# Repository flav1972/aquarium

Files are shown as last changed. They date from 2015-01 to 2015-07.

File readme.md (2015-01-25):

Aquarium controler
==================

Project Homepage: http://wiki.flav.com/wiki/Aquarium_Controller

Repository Contents
-------------------

* **/** - The root directory contains the arduino sketch
* **/hardware** - All hardware design files
* **/software** - Libraries used and hardwares sketch tests
* **/other** - Calculation and documentation files

Usage
-----

The project needs to be in a "aquarium" directory.

The main file is aquarium.ino. This is the file that has to be opened with Arduino IDE.

Edit setups in globals.h.

License Information
-------------------
The hardware is released under [Creative Commons Share-alike 3.0](http://creativecommons.org/licenses/by-sa/3.0/).  
The firmware is released under the [MIT License](http://opensource.org/licenses/MIT).

Author: Flavius Bindea

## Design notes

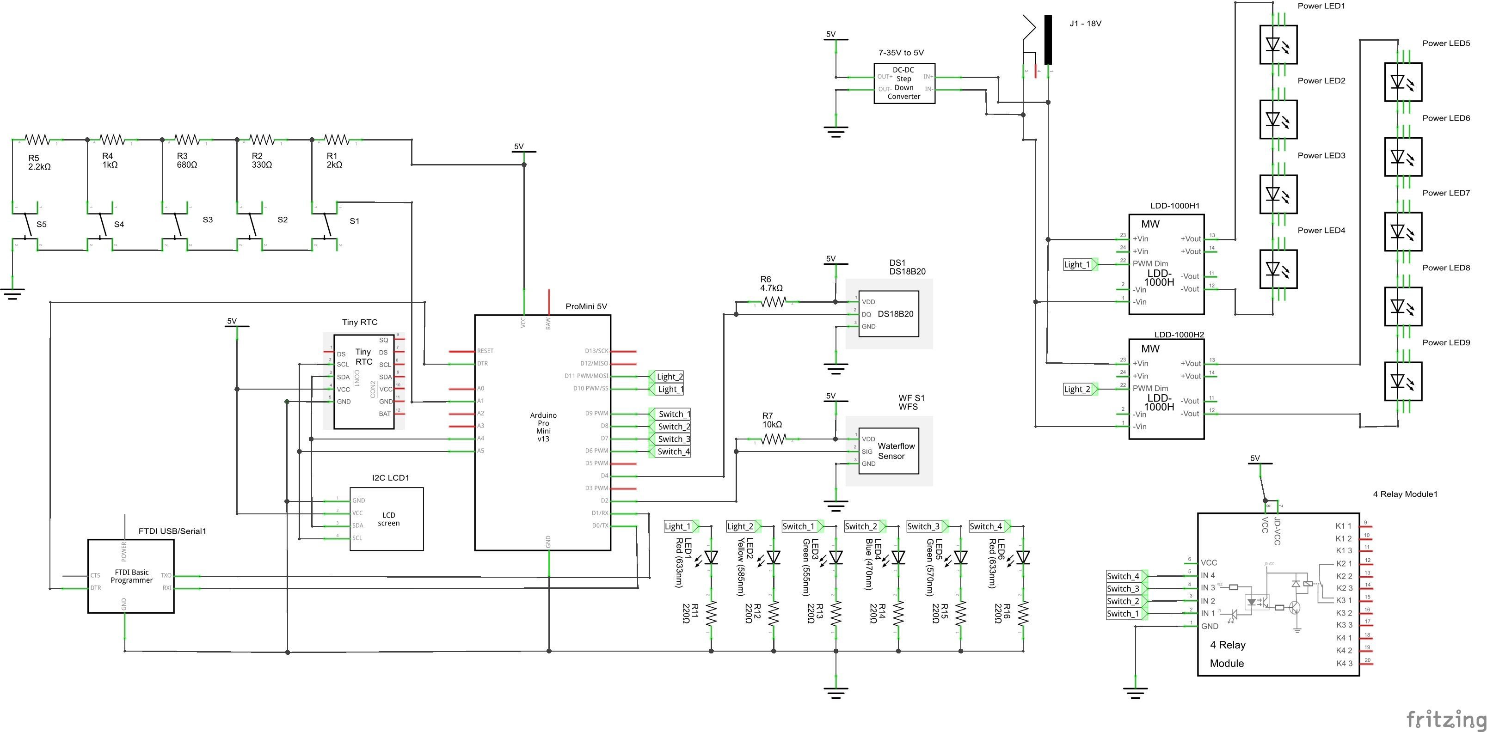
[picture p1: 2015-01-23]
hardware/aquarium_schema.png

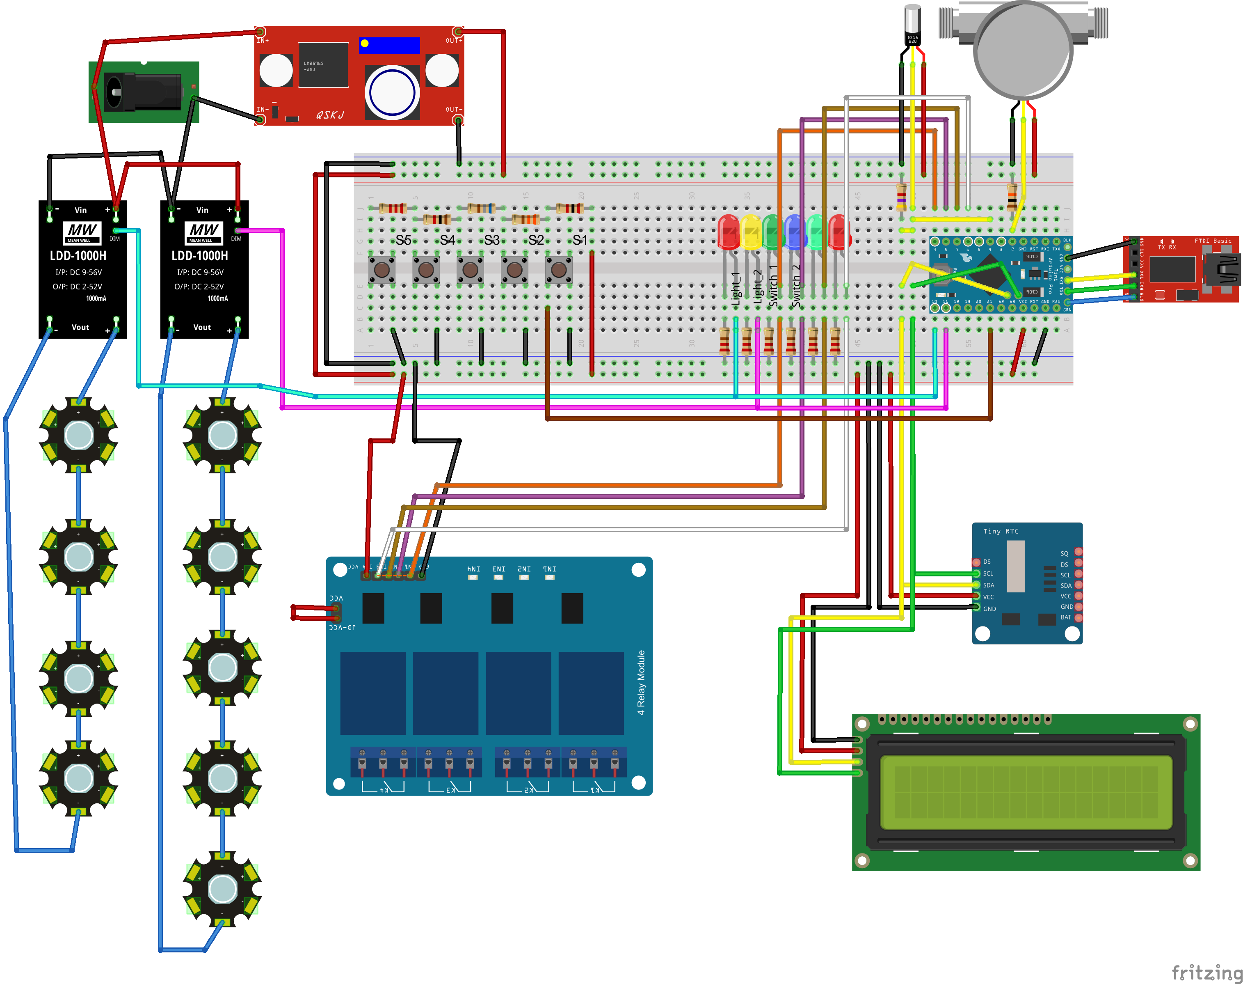
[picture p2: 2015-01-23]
hardware/aquarium_bb.png

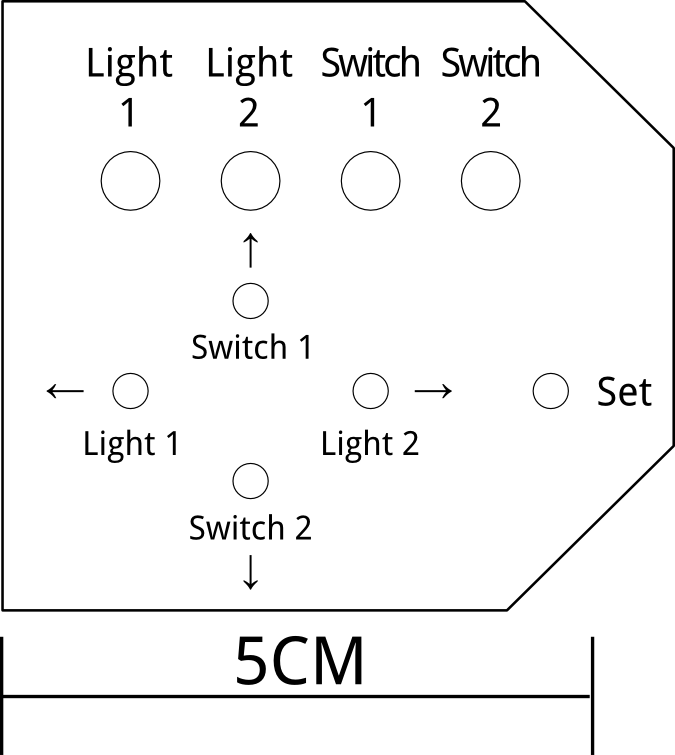
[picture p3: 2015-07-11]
other/front_pannel_labels.png

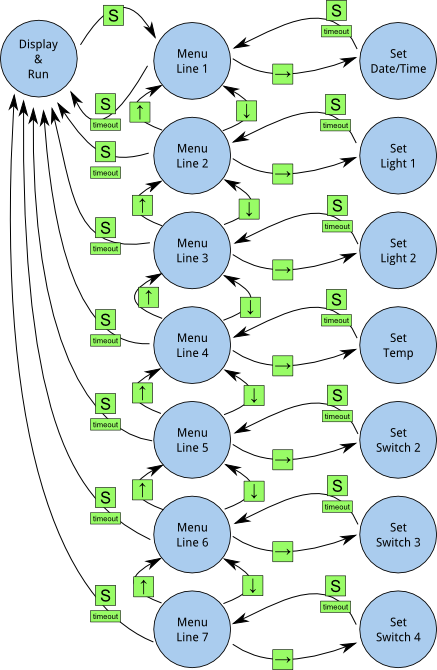
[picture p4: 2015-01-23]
other/menu.png

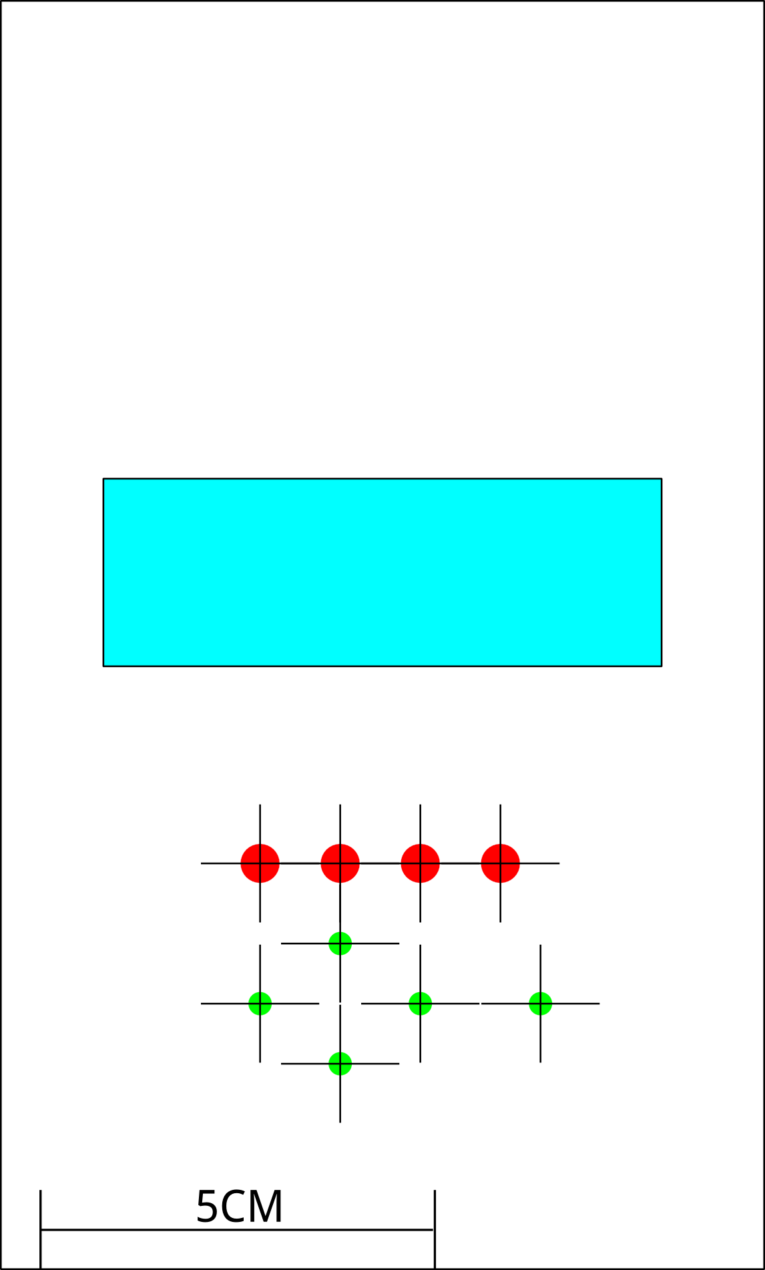
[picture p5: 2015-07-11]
other/front_pannel.png

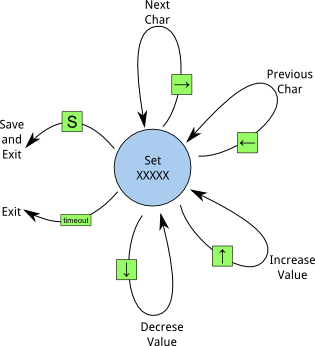
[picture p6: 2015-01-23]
other/menu_detail.png

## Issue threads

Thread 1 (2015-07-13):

DS18B20 fails after a few hours

flav1972, 2015-07-13:
The DS18B20 fails to send temperature after a few hours.
It looks like the same issue as this: http://forum.arduino.cc/index.php?topic=75757.0

The last commit about temperature does not solves the issue, neither the watchdog.

Need to implement cut/restart of power on the OneWire bus.

flav1972, 2016-01-28:
Fail is due to electric interferance with 220V motor near the controler.

Closed 2016-01-28.

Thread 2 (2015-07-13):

ERROR: temperature expired is never reached

flav1972, 2015-07-13:
It looks like : the following test is not correct.
    if(currentMillis - tempTimeLastRead > tempTimeMax) {
      Serial.println(F("ERROR: temperature expired"));

Must check "tempTimeMax" value.

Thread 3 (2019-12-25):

Which LCD Display

Alexxx2005, 2019-12-25:
Hello Flav,

what's the name from the Liquid LCD Display ?
It is with HD44780 or not can you give me the Name , please.

I have a 16X2 Display but she doesn't work :-(

Best Regards Alex

flav1972, 2019-12-25:
Hello,

yes it is. Same as : https://www.arduino.cc/en/Tutorial/HelloWorld?from=Tutorial.LiquidCrystal

Try the tutorial first.

There is some stuff here also: http://wiki.flav.com/wiki/Aquarium_Controller

Regards,
Flav

Alexxx2005, 2019-12-25:
Hello Flav

Thanks For you fast replay , i think my display is a China Clone, must buy a Real HD44780 16x2 Display and i hope it works

Merry Christmas , Alex

Alexxx2005, 2019-12-26:
Hello Flav,

now it work, i reinstall the complete Ardino IDE and than it's possible.

I have one question... It is possibe to make a Thunderstorm or Cloud
Simulation ?

Thunderstorm :  I could imagine that an LDD-1000 is switched off,
then immediately switched on and then back to the last dimming value

Best Regards Alex

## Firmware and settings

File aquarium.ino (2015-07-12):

/*
 
 Aquarium controler
 
 (C) 2014-2015 Flavius Bindea

Check history and latest versions on https://github.com/flav1972/aquarium

=============================================== 
Permission is hereby granted, free of charge, to any person obtaining a copy
of this software and associated documentation files (the "Software"), to deal
in the Software without restriction, including without limitation the rights
to use, copy, modify, merge, publish, distribute, sublicense, and/or sell
copies of the Software, and to permit persons to whom the Software is
furnished to do so, subject to the following conditions:

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
THE SOFTWARE IS PROVIDED "AS IS", WITHOUT WARRANTY OF ANY KIND, EXPRESS OR
IMPLIED, INCLUDING BUT NOT LIMITED TO THE WARRANTIES OF MERCHANTABILITY,
FITNESS FOR A PARTICULAR PURPOSE AND NONINFRINGEMENT. IN NO EVENT SHALL THE
AUTHORS OR COPYRIGHT HOLDERS BE LIABLE FOR ANY CLAIM, DAMAGES OR OTHER
LIABILITY, WHETHER IN AN ACTION OF CONTRACT, TORT OR OTHERWISE, ARISING FROM,
OUT OF OR IN CONNECTION WITH THE SOFTWARE OR THE USE OR OTHER DEALINGS IN
THE SOFTWARE.
===============================================

*/
#include <avr/pgmspace.h> // to put some strings in Flash
#include <avr/wdt.h> // includes watchdog defines
#include <Wire.h> // include the I2C library
#include <RTClib.h> // From: https://github.com/adafruit/RTClib.git 573581794b73dc70bccc659df9d54a9f599f4260
#include <EEPROM.h> // For read and write EEPROM
#include <OneWire.h>
#include <DallasTemperature.h>
#include <LCD.h>
#include <LiquidCrystal_I2C.h>
#include "globals.h"

// Initial setup
void setup() 
{
  int h, m;

  wdt_disable(); // disables watchdog

  Serial.begin(57600);
  Serial.println(F("Welcome to Aquarium Controler"));

#ifdef DEBUG
  Debug_RAM("setup start");
#endif

  // sets hall sensor for waterflow
  pinMode(hallsensor, INPUT); //initializes digital pin 2 as an input
  NbTopsFan = 0;   //Set NbTops to 0 ready for calculations
  FlowResetMillis = millis(); // gets the time
  attachInterrupt(0, rpm, RISING); //and the interrupt is attached
//  sei();      //Enables interrupts

  // initalise I2C interface  
  Wire.begin(); 
  
  // Configures RTC
  if (! RTC.isrunning()) {
    Serial.println(F("RTC is NOT running!"));
    // following line sets the RTC to the date & time this sketch was compiled
    RTC.adjust(DateTime(__DATE__, __TIME__));
  }

  // Start up DallasTemperature
  sensors.begin();
  sensors.getAddress(tempDeviceAddress, 0);
  sensors.setResolution(tempDeviceAddress, resolution);
  sensors.setWaitForConversion(false);  // request of temperature is non blocking
  sensors.requestTemperatures(); // sends command for all devices on the bus to perform a temperature conversion
  

  // Configures display
  // set up the number of columns and rows on the LCD 
  lcd.begin(cols, lines);

  // for liquid cystal the create chars have to be done after the lcd.begin. on some other libraries this has to be done before
  lcd.createChar(ch_up, up_bitmap);
  lcd.createChar(ch_down, down_bitmap);
  lcd.createChar(ch_set, set_bitmap);
  lcd.createChar(ch_deg, deg_bitmap);

  // Switch on the backlight
  lcd.setBacklightPin(BACKLIGHT_PIN,POSITIVE);
  lcd.setBacklight(HIGH);
  // Print a message to the LCD.
  lcd.setCursor(0, 0);
  lcd.print(F("Aquarium Controller"));

  // set the cursor to column 0, line 1
  // line 1 is the second row, since counting begins with 0
  lcd.setCursor(0, 1);
  // print to the second line
  lcd.print(F("RTC DS1307"));
  
  // if old EEPROM
  if(AQ_SIG1 == EEPROM.read(0) && AQ_SIG2_old == EEPROM.read(1)) {
    lcd.print(F(" OLD MEMORY"));
    EEPROM.write(1, AQ_SIG2);
    for(int i = 2+NBSETS_old*5; i < 2+NBSETS*5; i++)
      EEPROM.write(i, 0);
    write_eeprom_temp();
    write_eeprom_fading();
  }
  else if (AQ_SIG1 != EEPROM.read(0) || AQ_SIG2 != EEPROM.read(1)) {
    lcd.print(F(" NOT SET"));
    EEPROM.write(0, AQ_SIG1);
    EEPROM.write(1, AQ_SIG2);

    for(int i = 2; i < 2+NBSETS*5; i++)
      EEPROM.write(i, 0);
    write_eeprom_temp();
    write_eeprom_fading();
  }
  // reads the EEPROM setup
  for(int i = 0; i < NBSETS; i++)
    read_eeprom(i);
  read_eeprom_temp();
  read_eeprom_fading();

  // set output status modes
  pinMode(Status_Led, OUTPUT);

  for(int i = 0; i < NBSETS; i++)
    pinMode(out[i], OUTPUT);
    
  // Set initial state
  for(int i = 0; i < NBSETS; i++) {
    digitalWrite(out[i], 0); // Turn off 
  }
  digitalWrite(Status_Led, HIGH);

  now = RTC.now();
  h = now.hour();
  m = now.minute();
  // setup requested status
  for(int i = 0; i < NBSETS; i++) {
    out_m[i] = AUTO;
    if(i < SWITCHSET) {
      // last asked level and last level
      current_l[i] = asked_l[i]
                    = (unsigned int)(ti[i].power*255.0/99.0)*256 * in_on_timerange(i, h, m);
    }
  }    

  // sets temperature output control
  if(tempOutput != -1)
      out_m[tempOutput] = TMP;

  // smooth transition
  transitionSteps = transitionDuration / calculationInterval;
  incr_l = 255*256/transitionSteps;

  delay(1000);
  lcd.clear();

  // sets watchdog timeout to 4s
  wdt_enable(WDTO_4S);
#ifdef DEBUG
  Debug_RAM("setup end");
#endif
}

/*
** Main loop
*/
void loop() 
{
  int pressed_bt;

#ifdef DEBUG
  Debug_RAM("loop start");
#endif

  // resets watchdogtimer
  wdt_reset();

  // For interval determination
  unsigned long currentMillis = millis();

#ifdef DEBUG
  Serial.print(F("currentMillis = "));
  Serial.println(currentMillis);
#endif

  // reboot every day
  if(currentMillis > 86400000UL) {
    wdt_enable(WDTO_1S);
    delay(2000);
  }

  // we do something each interval 
  if(currentMillis - previousCalculationMillis > calculationInterval) {
#ifdef DEBUG
    Serial.println(F("calculations interval------------------------------"));
#endif
    // save lasted calculation millis
    previousCalculationMillis = currentMillis;  

    // does interval calculations
    calculations();
  }
  // only once an interval
  if(currentMillis - previousDisplayMillis > displayInterval) {
#ifdef DEBUG
    Serial.println(F("display interval------------------------------"));
#endif

    // save lasted display millis
    previousDisplayMillis = currentMillis;  

    // Serial output hour
    print_hour();
    Serial.println();

    // getting the voltage reading from the temperature sensor
    if(sensors.isConversionAvailable(tempDeviceAddress)) {
      temperatureC = sensors.getTempC(tempDeviceAddress);
      Serial.print(F("TEMPERATURE: ")); Serial.println(temperatureC);
      if(temperatureC < -55.0) {
        Serial.println(F("ERROR: temperature out of range"));
        tempOk = 0;
      }
      else {
        tempTimeLastRead = currentMillis;
        tempOk = 1;
      }
    }
    else {
      Serial.println(F("ERROR: no temperature available"));
    }
    if(currentMillis - tempTimeLastRead > tempTimeMax) {
      Serial.println(F("ERROR: temperature expired"));
      tempOk = 0;
      // reset temperature sensor
      Serial.println(F("RESET TEMPERATURE SENSOR"));
      sensors.begin();
      sensors.getAddress(tempDeviceAddress, 0);
      sensors.setResolution(tempDeviceAddress, resolution);
      sensors.setWaitForConversion(false);  // request of temperature is non blocking
    }
    sensors.requestTemperatures(); // sends command for all devices on the bus to perform a temperature conversion

    // display the data on the screen
    display_data();
  } 

  pressed_bt = read_button();

  switch(pressed_bt) {
    case BT_SET:
      lcd.blink();
      do_menu();
      lcd.noBlink();
      // clean up the screen
      lcd.clear();
      break;
    case BT_LEFT:
      switch_out(0);
      break;
    case BT_RIGHT:
      switch_out(1);
      break;
    case BT_UP:
      switch_out(2);
      break;
    case BT_DOWN:
      switch_out(3);
      break;
  }
    
  // small delay
  delay(50);
}

/*
** does interval calculations
*/
void calculations()
{
  int h, m;
#ifdef DEBUG
  Debug_RAM("calculations start");
#endif

  // read the date  
  now = RTC.now();
  h = now.hour();
  m = now.minute();
  
//  Serial.print(F("Nb of steps:"));
//  Serial.println(transitionSteps);
  
  // setting the status of the outputs
  for(int li = 0; li < NBSETS; li++) {
//    Serial.print(F("Calculation for "));
//    Serial.println(li);

//    Serial.print(F("Setup: "));
//    Serial.print(ti[li].h1);
//    Serial.print(':');
//    Serial.print(ti[li].m1);
//    Serial.print(F(" to "));
//    Serial.print(ti[li].h2);
//    Serial.print(':');
//    Serial.print(ti[li].m2);
//    Serial.print(F(" pow:"));
//    Serial.println(ti[li].power);

    byte out_s;
    if(out_m[li] == OFF)
      out_s = OFF;
    else if(out_m[li] == ON)
      out_s = ON;
    else if(out_m[li] == MAX)
      out_s = MAX;
    else if(out_m[li] == TMP) {
      // first check if temperature is corectly read
      if(tempOk) {
        // basic temperature regulation
        if (temperatureC > (tempSetpoint+tempTreshold)) {
          out_s = OFF;
          tempStatus = 0;
        }
        else if(temperatureC < (tempSetpoint-tempTreshold)) {
          out_s = ON;
          tempStatus = 1;      
        }
        else {
          out_s = (tempStatus == 1) ? ON : OFF;
        }
      }
      else {
        // temperature is not ok, turning of
        out_s = OFF;
        tempStatus = 0;
      }
    }
    else {
      // Auto time schedule
      
      // checking if we are in the ON time period
      if(in_on_timerange(li, h, m))
        out_s = ON;
      else
        out_s = OFF;
    }
    
//    Serial.print(F("calculation gives (0=OFF,1=AUTO,2=ON,3=MAX): "));
//    Serial.println(out_s);
     
    // if it is a light
    if(li < SWITCHSET) {
//      Serial.print(F("Calculation for "));
//      Serial.println(li);
//      Serial.print(F("Increment = "));
//      Serial.println(incr_l);
      switch(out_s) {
        case OFF:
          asked_l[li] = 0;
          break;
        case ON:
          asked_l[li] = (unsigned int)(ti[li].power*255.0/99.0)*256;
          break;
        case MAX:
          asked_l[li] = 255*256;
          break;
      }
//      Serial.print(F("Asked Level = "));
//      Serial.print(asked_l[li]);

//      Serial.print(F(", Current Before = "));
//      Serial.println(current_l[li]);
      
      if(current_l[li] < asked_l[li]) {
        if((asked_l[li] - current_l[li] ) < incr_l) {
//          Serial.println(F("==============Last  increasing"));
          current_l[li] = asked_l[li];          
        }
        else
          current_l[li] += incr_l;
      }
      else if(asked_l[li] < current_l[li]) {
        if((current_l[li] - asked_l[li]) < incr_l) {
//          Serial.println(F("==============Last  decreasing"));
          current_l[li] = asked_l[li];          
        }
        else
          current_l[li] -= incr_l;
      }
//      Serial.print(F("Current After = "));
//      Serial.println(current_l[li]);
//      Serial.print(F("Writing = "));
//      Serial.println(current_l[li]/256);
      // usign logarithmic perception table
      analogWrite(out[li], pgm_read_byte(&perception[current_l[li]/256]));
    }
    else {
      if(out_s == OFF) {
        digitalWrite(out[li], LOW);
//        Serial.println(F("putting OFF"));
      }
      else {
        digitalWrite(out[li], HIGH);
//        Serial.println(F("putting ON"));
      }
    }
  }
}

/**
 * calculates if we are in on period
 * @param li the number of the output
 * @param h hour
 * @param m minute
 * @return true if on, false if off
 */
boolean in_on_timerange(int li, int h, int m)
{
  // checking if we are in the ON time period
  // first we check if start time is earlier than end time
  byte order = ((ti[li].h2 > ti[li].h1) || (ti[li].h1 == ti[li].h2 && ti[li].m2 >= ti[li].m1)) ? 1 : 0;
  // order = 1 if time end is higher than time start

  // checks if current hour is in the ON interval
  if( (order && (h > ti[li].h1 || (h == ti[li].h1 && m >= ti[li].m1)) && (h < ti[li].h2 || (h == ti[li].h2 && m <= ti[li].m2))) 
            // start time <= current time and current time <= end time
    || (!order && ((h > ti[li].h1 || (h == ti[li].h1 && m >= ti[li].m1)) || (h < ti[li].h2 || (h == ti[li].h2 && m <= ti[li].m2))))
            // current time >= start time or current time <= end time
    )
    return true;
  return false;
}

/*
 * this displays the data on the screen 
 */
void display_data()
{
  int flow;

#ifdef DEBUG 
  Debug_RAM("display data");
#endif 

  // Gets RTC Time
  now = RTC.now();

  // set the cursor to column 0, line 0     
  lcd.setCursor(0, 0);

  // Print time
  print2dec(now.hour());
  lcd.print(':');
  print2dec(now.minute());
  lcd.print(':');
  print2dec(now.second());

  // Prints statuses, display_out moves the cursor
  for(byte i = 0; i < NBSETS; i++) {
    display_out(i);
  }
  
  // set the cursor to column 0, line 1
  lcd.setCursor(0, 1);

  // Now prints on LCD
#ifdef BIGSCREEN
  lcd.print(F("T:"));
#endif
  if(tempOk && (temperatureC > 0 && temperatureC < 100)) {
    lcd.print((int)temperatureC);
    lcd.print('.');
    lcd.print((int)((temperatureC-(int)temperatureC)*10.0+0.5));
    lcd.write(ch_deg);
    lcd.write('C');
    lcd.write(' ');
  }
  else
    lcd.print(F("ErrorT "));

  // prints temperature output status
  lcd.print(tempStatus);
    
  // set the cursor to column 10, line 1
#ifdef BIGSCREEN
  lcd.setCursor(11, 1);
  lcd.print(F("F:"));
#else
  lcd.setCursor(10, 1);
#endif
  // displays the flow
  flow = get_flow();
  Serial.print(F("FLOW: ")); Serial.println(flow);
  print3dec(flow);
  lcd.print(F("L/H"));
  
#ifdef BIGSCREEN
  lcd.setCursor(0, 3);
  // print date
  print2dec(now.day());
  lcd.print('/');
  print2dec(now.month());
  lcd.print('/');
  lcd.print(now.year());
#endif
}

// switch out put mode
void switch_out(byte n)
{
  switch(out_m[n]) {
    case OFF:
      out_m[n] = AUTO;
      break;
    case AUTO:
      out_m[n] = ON;
      break;
    case ON:
      out_m[n] = MAX;
      break;
    case MAX:
      out_m[n] = OFF;
      break;
  }
  display_out(n);
}

void display_out(byte i)
{
  lcd.setCursor(10+i, 0);
  switch(out_m[i]) {
    case OFF:
      lcd.print('0');
      break;
    case AUTO:
      lcd.print('A');
      break;
    case ON:
      lcd.print('1');
      break;
    case MAX:
      lcd.print('M');
      break;
    case TMP:
      lcd.print('T');
      break;
  }        
}

void print2dec(int nb) 
{ //this adds a 0 before single digit numbers
  if (nb >= 0 && nb < 10) {
    lcd.write('0');
  }
  lcd.print(nb);
}

void print3dec(int nb) 
{ //this adds a 0 before single digit numbers
  if(nb >= 0 && nb < 1000) {
    if (nb < 100) {
      lcd.write('0');
    }
    if (nb < 10) {
      lcd.write('0');
    }
    lcd.print(nb);
  }
  else
    lcd.print(F("Err"));
}

/**
 * Prints the hour on Serial
 */
void print_hour()
{
  Serial.print(now.hour());
  Serial.print(':');
  Serial.print(now.minute());
  Serial.print(':');
  Serial.print(now.second());
}

/**
 * this funtction returns free RAM
 * @return free RAM
 */
int freeRAM()
{
  extern int __heap_start, *__brkval;
  int v;
  return (int) &v - (__brkval == 0 ? (int) &__heap_start : (int) __brkval);
}

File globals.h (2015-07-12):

/*
 *  uncomment this to disable debug messages
 */
//#define DEBUG

/*
 * Debugging prototype
 */
#define Debug_RAM(X)   Serial.print(F(X " free RAM: ")); Serial.println(freeRAM())

// used for RTC
const int dayspermonth[] = { 31,28,31,30,31,30,31,31,30,31,30,31 };
RTC_DS1307 RTC;
DateTime now;

/****************************************************************************
 * I2C LCD setups
 */
// Define I2C Address where the PCF8574A is. Use i2c_scanner.ino to find it.
//#define I2C_ADDR    0x27  // my big screen's address
#define I2C_ADDR    0x3F  // my little screen's address

// if big screen (20x4) uncoment following line
//#define BIGSCREEN

// pins as connected on the PCF8574A
#define BACKLIGHT_PIN     3
#define En_pin  2
#define Rw_pin  1
#define Rs_pin  0
#define D4_pin  4
#define D5_pin  5
#define D6_pin  6
#define D7_pin  7
LiquidCrystal_I2C	lcd(I2C_ADDR,En_pin,Rw_pin,Rs_pin,D4_pin,D5_pin,D6_pin,D7_pin);

/*****************************************************************************
 * characters bitmaps
 */
// 126: -> 127: <-
const char ch_right = 126;
const char ch_left = 127;

const char ch_up = 1;
byte up_bitmap[8] = {
  B00100,
  B01110,
  B10101,
  B00100,
  B00100,
  B00100,
  B00100,
  B00000,
};

const char ch_down = 2;
byte down_bitmap[8] = {
  B00100,
  B00100,
  B00100,
  B00100,
  B10101,
  B01110,
  B00100,
  B00000
};

const char ch_set = 3;
byte set_bitmap[8] = {
  B10001,
  B01110,
  B01000,
  B01110,
  B00010,
  B01110,
  B10001,
  B00000
};

const char ch_deg = 4;
byte deg_bitmap[8] = {
  B01110,
  B01010,
  B01110,
  B00000,
  B00000,
  B00000,
  B00000,
  B00000,
};

/*****************************************************************************
 * temperature reader based on DS18B20
 */
// Data wire is plugged into pin 4 on the Arduino
#define ONE_WIRE_BUS 4

// Setup a oneWire instance to communicate with any OneWire devices 
// (not just Maxim/Dallas temperature ICs)
OneWire oneWire(ONE_WIRE_BUS);
 
// Pass our oneWire reference to Dallas Temperature.
DallasTemperature sensors(&oneWire);

DeviceAddress tempDeviceAddress; // address of the Temperature sensor
int  resolution = 10;	// 10 bits means 0.25°C increments conversion duration
                      // is 187.5ms

float temperatureC;   // the temperature from the sensor
byte tempOk = 0;            // is the temperature read ok ?
unsigned long tempTimeLastRead = 0;   // last time temperature was read
const unsigned long tempTimeMax = 60*1000;  // temperature read is valid for this duration (ms)
float tempSetpoint = 22;		// the temperature we need
float tempTreshold = 0.5;   // the treshold
int tempOutput = -1;  // the switch on which the temperature is controled
byte tempStatus = 0;  // status of the temperature switch

//////////////////////////////////////////////////////////
// Waterflow using hall sensor
volatile int NbTopsFan; //measuring the rising edges of the signal
unsigned long FlowResetMillis; // last reset
int hallsensor = 2;    //The pin location of the sensor

/*****************************************************************************
 * Buttons reading constants and variables
 */
const int buttonsPin = A1;	  // Pin on which the buttons are connected
const unsigned long debounceDelay = 10;   // debouncing delay
const unsigned long repeatDelay = 300;    // auto button repeat delay

// change value depending on your measurements
const int button1max = 75;		// reading should be 0, 75 threshold
const int button2max = 250;   // reading should be 151, from 76 to 250
const int button3max = 430;   // reading should be 347, from 251 to 430
const int button4max = 606;   // reading should be 515, from 431 to 606
const int button5max = 850;   // reading should be 700, from 607 to 850

// button values
#define BT_NONE 0
#define BT_SET 1
#define BT_LEFT 2
#define BT_RIGHT 3
#define BT_UP 4
#define BT_DOWN 5

/*****************************************************************************
 * Defines for Loops
 */
// For looping display by interval
unsigned long previousDisplayMillis = 0; 
const unsigned long displayInterval = 1000;
// For looping calculation by interval
unsigned long previousCalculationMillis = 0; 
const unsigned long calculationInterval = 250;

/*****************************************************************************
 *  display settings
 */
// screen size
#ifdef BIGSCREEN
const byte cols = 20, lines = 4;
#else
const byte cols = 16, lines = 2;
#endif

// menu of status
const int menumin = 0;
const int menumax = 8;

const char* menu_entry[] = {
  "1.Set Date/Time ",
  "2.Light 1 setup ",
  "3.Light 2 setup ",
  "4.Temp setup    ",
  "5.Switch 1 setup",
  "6.Switch 2 setup",
  "7.Switch 3 setup",
  "8.Switch 4 setup",
  "9.Fading long   ",
};

const unsigned long menuTimeout = 15000; // exit from menu after XXX ms

/*
 * Define the devices
 */
#define Light_1 10
#define Light_2 11
#define Switch_1 9
#define Switch_2 8
#define Switch_3 7
#define Switch_4 6

#define Status_Led 13

// this struct contains the time schedule of a position
struct AQTIME {
  byte h1;
  byte m1;
  byte h2;
  byte m2;
  byte power;
};

// number of setups in memory
#define NBSETS 6
#define LIGHTSET 0  // position of first light
#define SWITCHSET 2 // position of first switch = NB of lights
AQTIME ti[NBSETS];  // for each setup (output) we have a timeschedule
const byte out[] = { Light_1, Light_2, Switch_1, Switch_2, Switch_3, Switch_4 };

#define NBSETS_old 4	// old value for backwards compability

// statuses of outputs
#define OFF 0
#define AUTO 1
#define ON 2
#define MAX 3
#define TMP 4
byte out_m[NBSETS];

// for nice transition
unsigned long transitionDuration = 10000;
unsigned int transitionSteps;
unsigned int asked_l[SWITCHSET]; // new asked level (*256)
unsigned int current_l[SWITCHSET];  // current level multiplied by 
                                    //256 in order to avoid floating calculations
int incr_l; // step increment level multiplied by 256 in order to avoid floating calcultations
            // we are using only one increment for all transitions.
            // It is calculated to go from 0 to MAX in transitionDuration

// EEPROM signature for aquarium: they are stored in 0 and 1
const byte AQ_SIG1 = 45, AQ_SIG2 = 898;
const byte AQ_SIG2_old = 899; // old value of signature with only 4 sets
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

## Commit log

2014-04-22 first version with temperature not very stable
2014-04-22 changed to 3.3V reference: still not very stable need to make a calculation on several values
2014-04-23 added button read. needed to change reference back to 5V
2014-04-24 added button detection
2014-04-25 added move of cursor with the buttons
2014-05-01 added 4 leds
2014-05-04 added switch 1 and 2 setup and control
2014-05-04 added stop/start by buttons in main menu
2014-05-04 improuved buttons display
2014-05-27 Added Fritzling hardware design
    [aquarium.fzz]
2014-05-27 First version for publishing
    [aquarium.fzz]
2014-05-27 Revert "First version for publishing"
    This reverts commit abba5423b47a2709861a08d2faa94db4ab4729ab.
    [aquarium.fzz]
2014-05-27 Revert "Revert "First version for publishing""
    This reverts commit 94e4367133aea7b28268852c16bf2b75ef9917c1.
    [aquarium.fzz]
2014-05-30 Added labels
    [aquarium.fzz]
2014-10-05 added MeanWell LDD-1000H led driver
    [aquarium.fzz]
2014-10-05 Added the powerleds and leds driver.
    [aquarium.fzz]
2014-10-05 Added Power LEDs and LED drivers in all files.
    [aquarium.fzz]
2014-10-09 Added 4 Relay module
    [aquarium.fzz]
2014-10-09 Revert "Added 4 Relay module"
    This reverts commit 3a6c6f143c2a200c173f2394d4db838ff3d36a98.
    [aquarium.fzz]
2015-01-09 Started version 2: use Arduino Pro Mini, I2C LCD, new temperature sensor, water flow sensor
    [analog-key_calculation.xls]
2015-01-09 Revert "Revert "Added 4 Relay module""
    This reverts commit 7e3d89be7c5ff9a56c59973cc754dc3502a96adf.
    [aquarium.fzz]
2015-01-09 Revert "Test master"
    This reverts commit 61429c8ccd9c3ea873a594f10c96aed240979060.
    [aquarium.ino]
2015-01-09 added the DC/DC stepdown converter
    [aquarium.fzz]
2015-01-09 added testing of buttons on analog entry
2015-01-09 added testing of flow sensor
2015-01-12 started new hardware breadboard
    [aquarium.fzz]
2015-01-12 changed the precision of the temperature capture
2015-01-13 updated hardware for version 2
    [aquarium.fzz]
2015-01-13 changed LCD library and temperature sensor
2015-01-14 corrected createChar call for I2C Display
    [aquarium.ino]
2015-01-19 Added documentation files
    [analog-key_calculation.xls, screen.xls]
2015-01-19 Added sketch for waterflow calibration help.
2015-01-20 Changed menu. Added switch 1 menu entry
    [screen.xls]
2015-01-20 Added Flow measure. Renamed char bitmaps. Misc small changes.
2015-01-20 Changed button vars. added debouncing.
2015-01-20 Adde autorepet on button if key is keept pressed
2015-01-20 Simplified Button Analog read levels
2015-01-21 Reverted to SET button to exit main menu.
    [menus.ino]
2015-01-21 Change EEPROM for aditionnal devices
2015-01-22 Added store of temperature setups in EEPROM. Menu adds.
2015-01-22 Updated setup menus for big and small screen.
    [screen.xls]
2015-01-23 Corrected logic in schedule calculation. Update debug outputs.
    [aquarium.ino, flow.ino, globals.h]
2015-01-23 Added temperature control.
2015-01-23 Added perception table for LED level.
2015-01-23 Added setup in menu for fading duration of lights.
    [screen.xls]
2015-01-23 Removed some debug prints
2015-01-24 corrected bug in calculation: calculation of ON
    [aquarium.ino]
2015-03-08 Added DEBUG mode to display verbose messages on serial
    [screen.xls]
2015-03-08 Corected changing of Temperature output
2015-07-11 added front pannel print
2015-07-11 Added more controls on temperature read
2015-07-12 Added watchdog and reboot each 24h hours. This needs optiboot bootloader (already on Arduino UNO but Pro Mini has to be flashed).
    [aquarium.ino, globals.h, read_button.ino]
